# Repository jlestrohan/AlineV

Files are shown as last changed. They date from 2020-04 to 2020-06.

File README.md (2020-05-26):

# Alinea

### Autonomous Low Impact Networked Exploration Android

Protype built around:

- Caterpillar Chassis: https://www.ebay.fr/itm/292912268306

This device is aimed to map any indoor space, cartography its environment, 
while taking all sort of environmental datas, air quality, temperature, humidity,
etc...
Equipped with a 640x400 camera it can be effective in unaccessible areas as a
forefront explorer.

It is totally autonomous, althought it can be remotely controlled (Wifi/Bluetooth)
and will always try to control its whereabouts so that it can safely return back
to where it started.

#### Microcontrollers:

*  Nucleo STM32G474RE 172Mhz (main controller)
*  ESP32 (Wifi)
*  Alternate ESP8266 version

#### Sensors:

*  LM393 x2     Independant caterpillar speed sensors
*  SHR-04 x3    Ultrasonic Distance Sensors
*  CMPS12       Telemetry ToF magnetometer sensor
*  Buzzer       Start up music (not avail in esp8266 version))
*  BME280       Temperature/Humidity/Pressure
*  UV Leds simulating huge UV C lamps (200 ~ 280nm)

#### Batteries:
*  Lipo 4S/65C Battery for over one hour autonomy  

#### Motors:
*   2x PWM stepper motors controlling each caterpillar.

#### Displays:
*  16x2 LCD I2C Display module
  
#### Cloud/Gateway:
*  Able to send data over to it's gateway and/or MQTT endpoint
*  Video streaming included

### Main features
#### Autonomous behaviour
    The device is able to recon its environment. Once started it initializes 
    itself and starts mapping the region around him, and records any of it's 
    movement on a AWS Dynamodb. The datas are processed thru a graphical 
    interface (redash) that offers some visuals.
    
It's integrated movement detection device makes it a perfect candidate for 
security patrol device which is then able to patrol along a predefined path or 
totally autonomously.

The motors are intelligently controlled so the device can respond to about every
critical event that can happen:

    * it will detect any derivation from the current heading and adjust its 
        trajectory accordingly until it meets an obstacle.if one of the caterpillar 
        is skidding for some reason and the android is starting to lose its heading,
        it will detect the fault and try to correct its trajectory by regulating 
        the motors power accordingly, guided by its inbuilt CMPS12 mag sensor
    *  it is able to record every single movement it makes so it is easy for it to
        just turn back and come back to a previous location with a relatively good
        accuracy (not implemented yet)
    * Once an obstacle has been detected from the front or rear sensors (bound to
        where it's actually headed) it will compute the best directional decision to 
        take next according to the side sensors data.
    * if it meets some kind of hole or dangerous terrain that could have dire 
        consequences upon the mission, it will try to avoid the obstacle and keep
        the previous heading once the obstacle have been overtaken, thanks to a 
        couple of obstacle sensors located underneath the chassis that will guard
        the device from falling from too height for instance. Thus it will also 
        deactivate if it detects any lift off or any foreign action taken against
        it, while keeping the video monitor active (if previously setup)
    * To preserve a constant speed and guarantee an accurate mapping of the place it
        is operating in, the device is equipped with a gyroscope/accelerometer that
        will let it adjust its speed either on flat or upward/downward sloping 
        terrains for instance. It will also detect it's current levelling and adapt
        the datas accordingly.
    * according to what has been defined when the device was setup and started, it can adopt
        different behaviours according to any event that may occur:
        
        ie:
            1.  one of the environmental sensor gets some critical values, is offline...
            2.  battery getting low, shall it return or stop ?
            3.  mapping completed, no known unmapped surface left, mapping lost...
            4.  control command received from the remote operator
            5.  data processing compromised (SD card full, no connectivity..)
            6.  movement or dire condition detected that requires human intervention
            7.  in the case of patrol mode, detection of some unattended event...
            etc...
            
    To be continued, edited.. and coded.... this project is far from over but 
    still in a very presentable way.
        
        Beside robotics, it is a real connected thing!

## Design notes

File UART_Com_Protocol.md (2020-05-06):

# UART Communication protocol

### Protocol convention for com between STM32 and ESP8266

Custom and simplified Implementation of the HDLC Protocol (High-Level Data Link Control).
The communication between the STM32 and the ESP32 is a full-duplex bi-directional
data exchange "best-effort" mode (for now).

However as the lines between both MCU are very short, fixed, and thus very little prone to errors,
all the coding eforts are currently focused on data transmission to the cloud, and building the IA.

Encapsulated data is serialized JSON data:

#### Commands:

All datas/commands/sensors id etc..  MUST be defined each side and double checked.
For the sake of a lighter payload we just send very little information thru the UART.
Bitwise flags are used to be able to send several commands to several devices in a single
communication process.

Any MCU is able to either send data on its own. In the case of the STM32 we consider
that every data sent out of request is something he asks the ESP32 to relay to the cloud, unless
previously asked by the ESP32.

### General
    ##### Devices infos (variables included in all JSON)
    
    TIMESTAMP       (if no NTP is available at any point, this field will be -1 - both devices share the same clock, stm32 requests the esp anytime to have this updated)
    DEVICE_UUID     32 bits UUID
    UPTIME          in ms ticks

### STM32 
    ##### Addressable Devices: (uint16_t DeviceFlag)
    
        MOTOR_LEFT              =   1 << 0      /* control & speed info */
        MOTOR_RIGHT             =   1 << 1      /* control & speed info */
        FRONT_ULTRASONIC        =   1 << 2      /* control (on/off) & data (beware the fast acquisition vs the slow transmission) */
        BACK_ULTRASONIC         =   1 << 3      /* see above */
        BOTTOM_ULTRASONIC       =   1 << 4      /* see above */
        FRONT_SENSOR_SERVO      =   1 << 5      /* control & position (pwm value) */
        BMP280_SENSOR           =   1 << 6      /* control (on/off) & pressure information */
        MPU6050_SENSOR          =   1 << 7
        SDCARD_DEVICE           =   1 << 8      /* read file, status, control */     
        LED_ONBOARD             =   1 << 9
        LED_UART_EXTERNAL       =   1 << 10
        
        CORE_SYSTEM_STATUS      =   1 << 14     /* when requested infos are temperature, device uuid, active threads, avg load, uptime, etc etc... */
        CORE_SYSTEM_DEEPSLEEP   =   1 << 15     /* special flag, will take precedence over all the rest, when received the device goes into deepsleep mode!! */
        
### ESP32
    ##### Addressable Devices: (uint16_t DeviceFlag)
    
        BUZZER_DEVICE           =   1 << 0      /* play tune command essentially */
        
        CORE_SYSTEM_DATA        =   1 << 14     /* when requested infos are temperature, device uuid, active threads, avg load, uptime, etc etc... */
        CORE_SYSTEM_DEEPSLEEP   =   1 << 15     /* special flag, will take precedence over all the rest, when received the device goes into deepsleep mode!! */

### Common Actions: 
    ##### Actions(uint16_r cmdActionsFlag)
    
        CONTROL_OFF             =   1 << 0      /* Commands the device to turn on */
        CONTROL_ON              =   1 << 1      /* Commands the device to turn off - Beware, nav control will always have the last word. If you ask the bottom sensor 
                                                    to turn off, the Nav Control will immediately stop the engines to avoid putting the robot in a situation of danger.
                                                    Also, if you command the right motor to turn off, the robot will not hit something left if it detects an obstacle */
        REQ_STATUS              =   1 << 2      /* requests a full status, payload may vary according to the available data */
        REQ_DATA                =   1 << 3      /* requests data acquisition & transmission for the selected device(s)
        SEND_DATA               =   1 << 4      /* Informs the device that arguments are available along with the command.. ie Buzzer, play tune 6
        REQ_READY               =   1 << 5      /* requests the other MCU if it is ready to accept communications - adapt code accordingly */
        ACK_READY               =   1 << 6      /* acknowledge ready status */
        
### JSON Example:

    STM to >ESP32 example:
    {
        "Timestamp":    1588746512,
        "Uptime":   124098,
        deviceFlag: 1,      /* buzzer */
        actionFlags: 4,     /* we send data to the device */
        data:[
            "playtune": 3   /* will command the device to play tune 3 */
        ]

    to be edited ...
{

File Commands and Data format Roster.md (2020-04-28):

## ESP32 <-> STM32 Commands and Data format Roster

Aside from the proprietary protocol used to let both micro-controllers share data in a full duplex bi-directional way, the following conventions have been setup:

### commands:

All commands are to be included between [CMD:(sha256)] **command here** [/CMD] tags

##### <u>emitted by the STM32 to ESP32:</u>

* **tune** *tunetype* *prioritary*
  *  will command the ESP32 to play the selected tune. 
  * *tunetype*: (string) name of the tune
  * *prioritary*: if true, this flag will order the ESP32 to immediately play the tune even if something else is playing
* **tune** *tunelist* - will command the ESP32 to send back an array of the tunes available
  * tunelist: keyword

##### <u>emitted by the ESP32 to STM32:</u>

- **restart**
  - restarts the rover, going thru all initialization process
- **sleep**
  - commands the STM32 to go into deepsleep mode to save battery
  - will be woke up either by a press on the user button, either any event incoming via network still to be defined
  - that command will also be invoked when the LiPo battery sensor detects a weak battery, in order to avoid the destruction of the lipo's cells. In such case a recognizable tune will also be played by the buzzer to inform the driver that the Lipo has to be changed.
- **wakeup**
  - commands the STM32 to exit deepsleep mode and become fully operational again
* **motion** *forward/backward* *milliseconds* *<u>speed</u>*
  * commands the rover to start moving backward or forward for x millis at the optional speed between 1 to 100 (0 will return a bad command error)
* **motion** *left/right millis <u>speed</u>*
  * commands the rover to start turning left or right for x millis at the optional speed 1-100 (0 would return a bad command error)
* **motion** *azimuth milliseconds <u>speed</u>*
  * commands the rover to start moving toward the azimuth given in degrees (magnetic) for x millis at the speed of (1-100, 0 returning a bad command error)
* **motion** *stop*
  * will immediately stop the rover commanding the motors to idle

    All motion commands will still be driven by the obstacle detection sensors and the rover will never endanger itself, thus stopping itself even if it has 
    been commanded to move. 
  
* **lcd** *clear*
  * clears the LCD display
* **lcd** *cursor X Y*
  * sets LCD cursor to X Y
* **lcd** *print text*
  * prints "text" to the display, trimming anything over 16 chars

### datas:

All commands are to be included between [DTA:(sha256)] **{json data here}** [/DTA] tags. 

Datas are JSON preformatted and ready to be passed to the ESP32 for direct forwarding to MQTT service thru communication protocols available (BLE, BT, WiFi etc..)

No data is sent from the ESP32 to the STM32, all eventual data needed is included in the commands if applicable.

All SHA256 calculations are made counting every character included between the tags with brackets.

json format for STM general status:

```
{"STATE": {
	"timestamp": 1588046942,
	"free_heap": 2140,
    "ram_used": 10354,
    "ram_free": 595026,
    "sensor_voltage": 5,
    "core_temp_c": 47,
    "firmware_version": "1.12c",
    "last_updated": "2020-04-28T05:13:48",
    "device_uuid": "123e4567-e89b-12d3-a456-426655440000",
    },
 } 

```

	json format for STM Sensor data (example)

```
{"DATA": {
	"timestamp": 1588046942,
    "device_uuid": "123e4567-e89b-12d3-a456-426655440000",
    "SENSOR": {
    		"sensorType": "gaz",
    		"module_id": "12BDE54",
    		"value": 23,
    		"unit": "C"
    	},
    },
 } 

```

		json format for STM ACK result:

```
{"RESULT": {
	"timestamp": 1588046942,
    "device_uuid": "123e4567-e89b-12d3-a456-426655440000",
    "RESULT": {
    		"command": "motion forward 15000",
    		"result": "completed",
    		"time_completed_ms": 23254,
    	},
    },
 } 

```

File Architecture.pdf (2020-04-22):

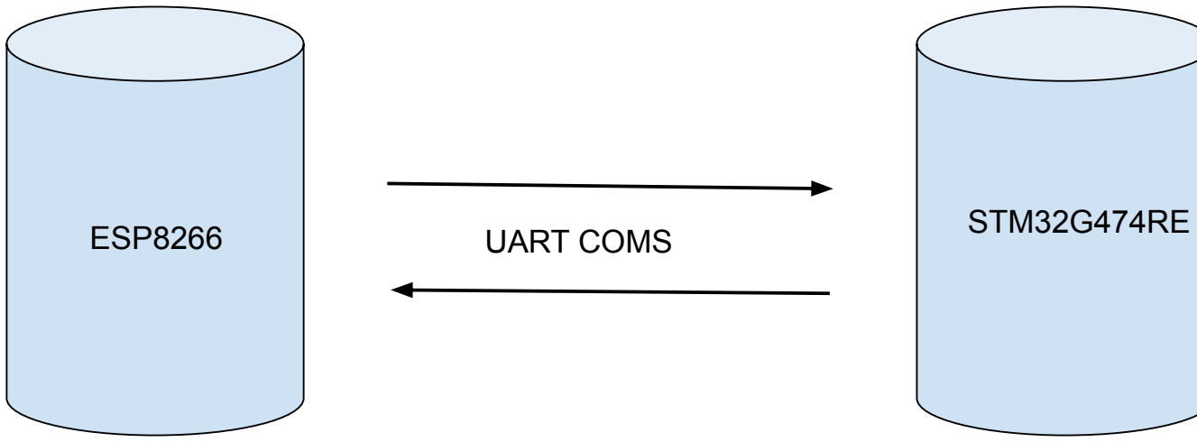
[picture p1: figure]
ESP8266; STM32G474RE UART COMS

TELNET

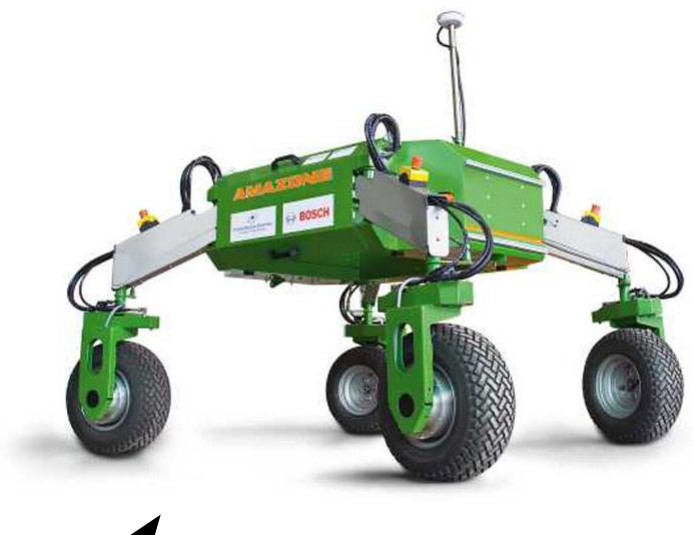
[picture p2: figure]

Motion Ctrl

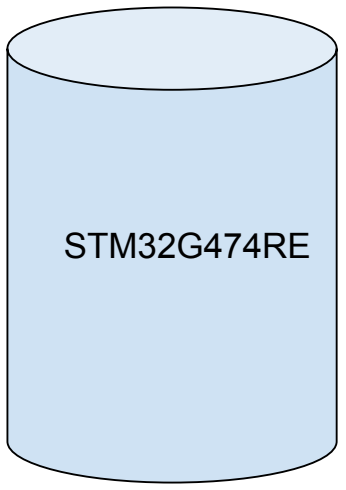
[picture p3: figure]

Sensors

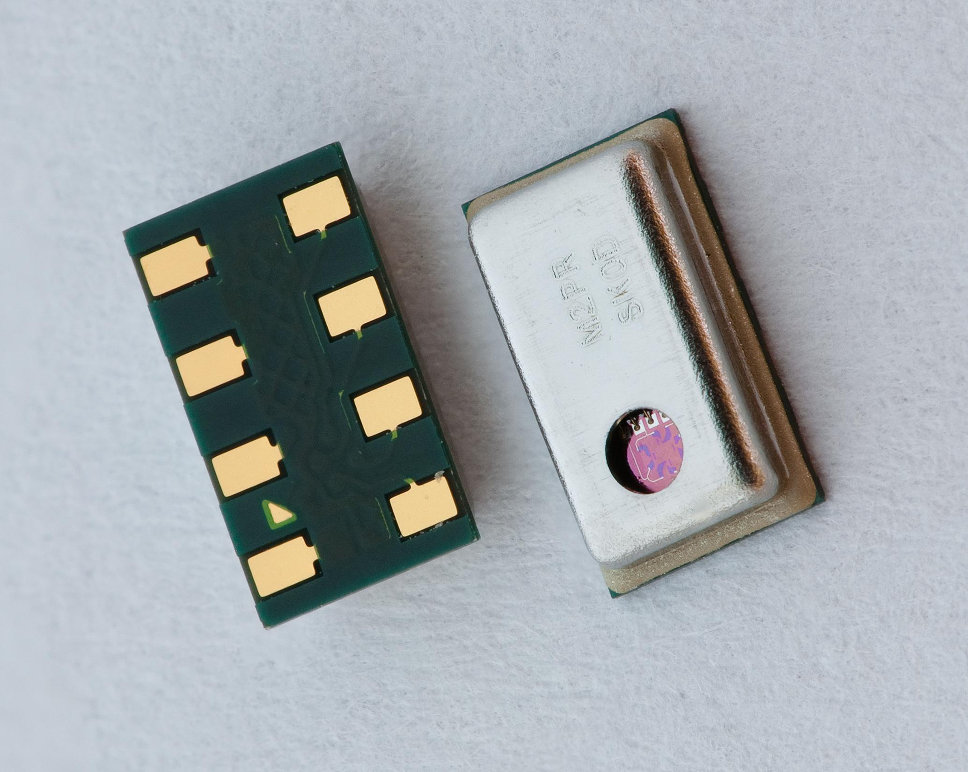
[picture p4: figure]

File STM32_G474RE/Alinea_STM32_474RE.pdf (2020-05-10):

## Alinea_STM32_474RE Project Configuration Report

# 1. Description

## 1.1. Project

Project Name | Alinea_STM32_474RE
Board Name | NUCLEO-G474RE
Generated with: | STM32CubeMX 5.6.1
Date | 05/08/2020

## 1.2. MCU

MCU Series | STM32G4
MCU Line | STM32G4x4
MCU name | STM32G474RETx
MCU Package | LQFP64
MCU Pin number | 64

# 2. Pinout Configuration

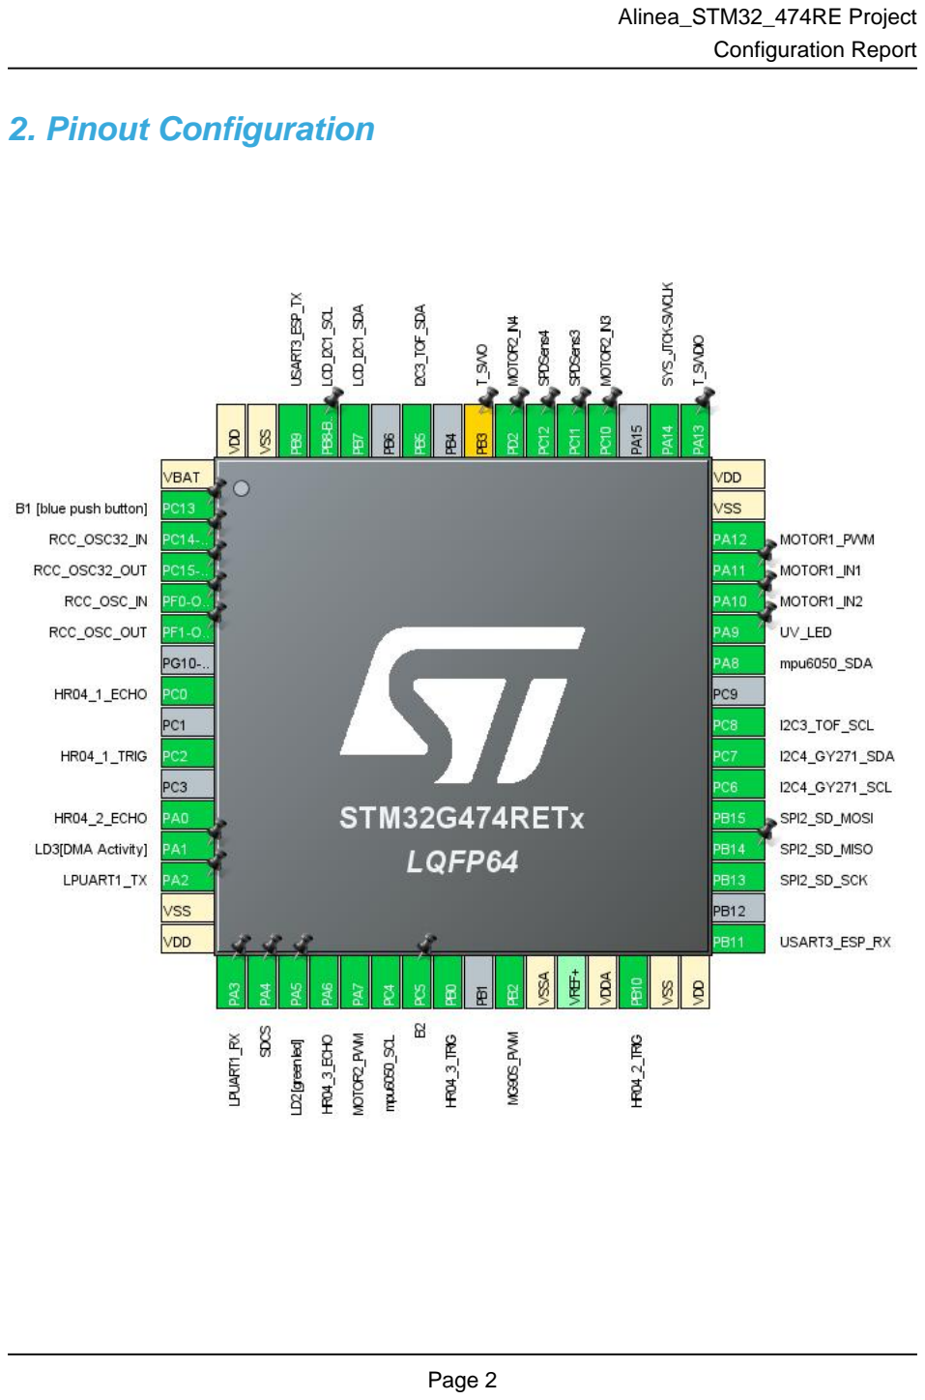
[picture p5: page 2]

# 3. Pins Configuration

Pin Number LQFP64 | Pin Name (function after reset) | Pin Type | Alternate Function(s) | Label
1 | VBAT | Power
2 | PC13 | I/O | GPIO_EXTI13 | B1 [blue push button]
3 | PC14-OSC32_IN | I/O | RCC_OSC32_IN
4 | PC15-OSC32_OUT | I/O | RCC_OSC32_OUT
5 | PF0-OSC_IN | I/O | RCC_OSC_IN
6 | PF1-OSC_OUT | I/O | RCC_OSC_OUT
8 | PC0 | I/O | TIM1_CH1 | HR04_1_ECHO
10 | PC2 | I/O | TIM1_CH3 | HR04_1_TRIG
12 | PA0 | I/O | TIM2_CH1 | HR04_2_ECHO
13 | PA1 * | I/O | GPIO_Output | LD3[DMA Activity]
14 | PA2 | I/O | LPUART1_TX
15 | VSS | Power
16 | VDD | Power
17 | PA3 | I/O | LPUART1_RX
18 | PA4 * | I/O | GPIO_Output | SDCS
19 | PA5 * | I/O | GPIO_Output | LD2 [green led]
20 | PA6 | I/O | TIM3_CH1 | HR04_3_ECHO
21 | PA7 | I/O | TIM17_CH1 | MOTOR2_PWM
22 | PC4 | I/O | I2C2_SCL | mpu6050_SCL
23 | PC5 | I/O | GPIO_EXTI5 | B2
24 | PB0 | I/O | TIM3_CH3 | HR04_3_TRIG
26 | PB2 | I/O | TIM5_CH1 | MG90S_PWM
27 | VSSA | Power
29 | VDDA | Power
30 | PB10 | I/O | TIM2_CH3 | HR04_2_TRIG
31 | VSS | Power
32 | VDD | Power
33 | PB11 | I/O | USART3_RX | USART3_ESP_RX
35 | PB13 | I/O | SPI2_SCK | SPI2_SD_SCK
36 | PB14 | I/O | SPI2_MISO | SPI2_SD_MISO
37 | PB15 | I/O | SPI2_MOSI | SPI2_SD_MOSI
38 | PC6 | I/O | I2C4_SCL | I2C4_GY271_SCL
39 | PC7 | I/O | I2C4_SDA | I2C4_GY271_SDA
40 | PC8 | I/O | I2C3_SCL | I2C3_TOF_SCL
42 | PA8 | I/O | I2C2_SDA | mpu6050_SDA
43 | PA9 * | I/O | GPIO_Output | UV_LED

Pin Number LQFP64 | Pin Name (function after reset) | Pin Type | Alternate Function(s) | Label
44 | PA10 * | I/O | GPIO_Output | MOTOR1_IN2
45 | PA11 * | I/O | GPIO_Output | MOTOR1_IN1
46 | PA12 | I/O | TIM16_CH1 | MOTOR1_PWM
47 | VSS | Power
48 | VDD | Power
49 | PA13 | I/O | SYS_JTMS-SWDIO | T_SWDIO
50 | PA14 | I/O | SYS_JTCK-SWCLK
52 | PC10 * | I/O | GPIO_Output | MOTOR2_IN3
53 | PC11 | I/O | GPIO_EXTI11 | SPDSens3
54 | PC12 | I/O | GPIO_EXTI12 | SPDSens4
55 | PD2 * | I/O | GPIO_Output | MOTOR2_IN4
56 | PB3 ** | I/O | SYS_JTDO-SWO | T_SWO
58 | PB5 | I/O | I2C3_SDA | I2C3_TOF_SDA
60 | PB7 | I/O | I2C1_SDA | LCD_I2C1_SDA
61 | PB8-BOOT0 | I/O | I2C1_SCL | LCD_I2C1_SCL
62 | PB9 | I/O | USART3_TX | USART3_ESP_TX
63 | VSS | Power
64 | VDD | Power

## * The pin is affected with an I/O function ** The pin is affected with a peripheral function but no peripheral mode is activated

# 4. Clock Tree Configuration

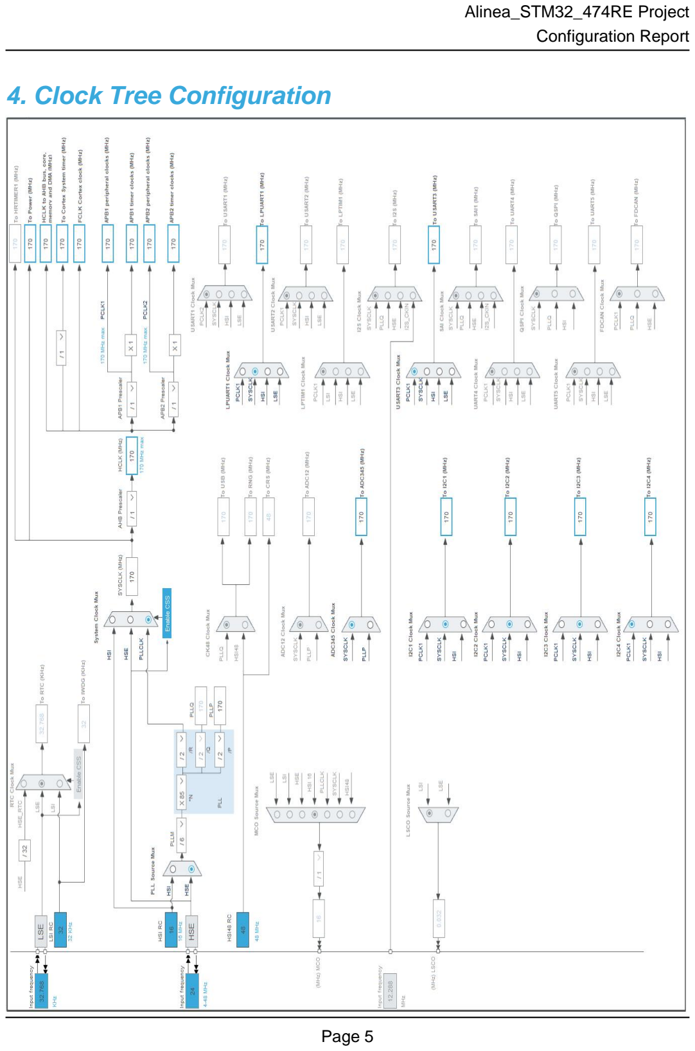
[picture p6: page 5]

# 5. Software Project

## 5.1. Project Settings

Name | Value
Project Name | Alinea_STM32_474RE
Project Folder | F:\Documents\STM32CubeWSP\alinea\STM32_G474RE
Toolchain / IDE | STM32CubeIDE
Firmware Package Name and Version | STM32Cube FW_G4 V1.2.0

## 5.2. Code Generation Settings

Name | Value
STM32Cube MCU packages and embedded software | Copy only the necessary library files
Generate peripheral initialization as a pair of '.c/.h' files | Yes
Backup previously generated files when re-generating | No
Delete previously generated files when not re-generated | Yes
Set all free pins as analog (to optimize the power consumption) | No

# 6. Power Consumption Calculator report

### 6.1. Microcontroller Selection

Series | STM32G4
Line | STM32G4x4
MCU | STM32G474RETx
Datasheet | DS12288_Rev0

### 6.2. Parameter Selection

Temperature | 25
Vdd | 3.0

### 6.3. Battery Selection

Battery | Li-SOCL2(A3400)
Capacity | 3400.0 mAh
Self Discharge | 0.08 %/month
Nominal Voltage | 3.6 V
Max Cont Current | 100.0 mA
Max Pulse Current | 200.0 mA
Cells in series | 1
Cells in parallel | 1

## 6.4. Sequence

Step | Step1 | Step2
Mode | RUN | STOP1
Vdd | 3.0 | 3.0
Voltage Source | Battery | Battery
Range | Range1-Boost | NoRange
Fetch Type | FLASH/DualBank/ART | NA
CPU Frequency | 170 MHz | 0 Hz
Clock Configuration | HSE BYP PLL | ALL CLOCKS OFF
Clock Source Frequency | 4 MHz | 0 Hz

### Peripherals

Additional Cons. | 0 mA | 0 mA
Average Current | 29.5 mA | 80.5 µA
Duration | 0.1 ms | 0.9 ms
DMIPS | 213.0 | 0.0
Ta Max | 124.25 | 129.98
Category | In DS Table | In DS Table

## 6.5. RESULTS

Sequence Time | 1 ms | Average Current | 3.02 mA
Battery Life | 1 month, 16 days, 9 hours | Average DMIPS | 212.5 DMIPS

## 6.6. Chart

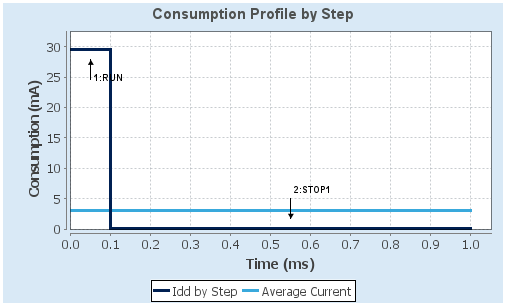
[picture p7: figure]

# 7. IPs and Middleware Configuration

# 7.1. ADC5

## mode: Temperature Sensor Channel mode: Vbat Channel mode: Vrefint Channel 7.1.1. Parameter Settings:

### ADC_Settings:

Clock Prescaler | Asynchronous clock mode divided by 1
Resolution | ADC 12-bit resolution
Data Alignment | Right alignment
Gain Compensation | 0
Scan Conversion Mode | Enabled
End Of Conversion Selection | End of single conversion
Low Power Auto Wait | Disabled
Continuous Conversion Mode | Enabled *
Discontinuous Conversion Mode | Disabled
DMA Continuous Requests | Disabled
Overrun behaviour | Overrun data preserved

### ADC_Regular_ConversionMode:

Enable Regular Conversions | Enable
Enable Regular Oversampling | Disable
Number Of Conversion | 3 *
External Trigger Conversion Source | Regular Conversion launched by software
External Trigger Conversion Edge | None
Rank | 1
Channel | Channel Temperature Sensor
Sampling Time | 92.5 Cycles *
Offset Number | No offset
Rank | 2 *
Channel | Channel Vbat *
Sampling Time | 92.5 Cycles *
Offset Number | No offset
Rank | 3 *
Channel | Channel Vrefint *
Sampling Time | 92.5 Cycles *
Offset Number | No offset

### ADC_Injected_ConversionMode:

Enable Injected Conversions | Disable

### Analog Watchdog 1:

Enable Analog WatchDog1 Mode | false

### Analog Watchdog 2:

Enable Analog WatchDog2 Mode | false

### Analog Watchdog 3:

Enable Analog WatchDog3 Mode | false

# 7.2. GPIO

# 7.3. I2C1

## I2C: I2C 7.3.1. Parameter Settings:

### Timing configuration:

Custom Timing | Disabled
I2C Speed Mode | Standard Mode
I2C Speed Frequency (KHz) | 100
Rise Time (ns) | 0
Fall Time (ns) | 0
Coefficient of Digital Filter | 0
Analog Filter | Enabled
Timing | 0x30A0A7FB *

### Slave Features:

Clock No Stretch Mode | Disabled
General Call Address Detection | Disabled
Primary Address Length selection | 7-bit
Dual Address Acknowledged | Disabled
Primary slave address | 0

# 7.4. I2C2

## I2C: I2C 7.4.1. Parameter Settings:

### Timing configuration:

Custom Timing | Disabled

I2C Speed Mode | Standard Mode
I2C Speed Frequency (KHz) | 100
Rise Time (ns) | 0
Fall Time (ns) | 0
Coefficient of Digital Filter | 0
Analog Filter | Enabled
Timing | 0x30A0A7FB *

### Slave Features:

Clock No Stretch Mode | Disabled
General Call Address Detection | Disabled
Primary Address Length selection | 7-bit
Dual Address Acknowledged | Disabled
Primary slave address | 0

# 7.5. I2C3

## I2C: I2C 7.5.1. Parameter Settings:

### Timing configuration:

Custom Timing | Disabled
I2C Speed Mode | Fast Mode *
I2C Speed Frequency (KHz) | 400
Rise Time (ns) | 0
Fall Time (ns) | 0
Coefficient of Digital Filter | 0
Analog Filter | Enabled
Timing | 0x10802D9B *

### Slave Features:

Clock No Stretch Mode | Disabled
General Call Address Detection | Disabled
Primary Address Length selection | 7-bit
Dual Address Acknowledged | Disabled
Primary slave address | 0

# 7.6. I2C4

## I2C: I2C

## 7.6.1. Parameter Settings:

### Timing configuration:

Custom Timing | Disabled
I2C Speed Mode | Standard Mode
I2C Speed Frequency (KHz) | 100
Rise Time (ns) | 0
Fall Time (ns) | 0
Coefficient of Digital Filter | 0
Analog Filter | Enabled
Timing | 0x30A0A7FB *

### Slave Features:

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

# 7.7. LPUART1

## Mode: Asynchronous 7.7.1. Parameter Settings:

### Basic Parameters:

Baud Rate | 115200 *
Word Length | 8 Bits (including Parity)
Parity | None
Stop Bits | 1

### Advanced Parameters:

Data Direction | Receive and Transmit
Single Sample | Disable
Prescaler | clock /1
Fifo Mode | FIFO mode disable
Txfifo Threshold | 1 eighth full configuration
Rxfifo Threshold | 1 eighth full configuration

### Advanced Features:

TX Pin Active Level Inversion | Disable
RX Pin Active Level Inversion | Disable
Data Inversion | Disable
TX and RX pins Swapping | Disable

Overrun | Enable
DMA on RX Error | Enable
MSB First | Disable

# 7.8. RCC

## High Speed Clock (HSE): Crystal/Ceramic Resonator Low Speed Clock (LSE) : Crystal/Ceramic Resonator 7.8.1. Parameter Settings:

### System Parameters:

VDD voltage (V) | 3.3
Instruction Cache | Enabled
Prefetch Buffer | Disabled
Data Cache | Enabled
Flash Latency(WS) | 8WS (7 CPU cycle)

### RCC Parameters:

HSI Calibration Value | 64
HSE Startup Timout Value (ms) | 100
LSE Startup Timout Value (ms) | 5000

### Power Parameters:

Power Regulator Voltage Scale | Power Regulator Voltage Scale 1 boost

### Peripherals Clock Configuration:

Generate the peripherals clock configuration | TRUE

# 7.9. SPI2

## Mode: Full-Duplex Master 7.9.1. Parameter Settings:

### Basic Parameters:

Frame Format | Motorola
Data Size | 8 Bits *
First Bit | MSB First

### Clock Parameters:

Prescaler (for Baud Rate) | 4 *
Baud Rate | 42.5 MBits/s *
Clock Polarity (CPOL) | Low

Clock Phase (CPHA) | 1 Edge

### Advanced Parameters:

CRC Calculation | Disabled
NSSP Mode | Enabled
NSS Signal Type | Software

# 7.10. SYS

## Debug: Serial Wire Timebase Source: TIM7 mode: save power of non-active UCPD - deactive Dead Battery pull-up

# 7.11. TIM1

## Slave Mode: Reset Mode Trigger Source: TI1FP1 Clock Source : Internal Clock Channel1: Input Capture direct mode Channel2: Input Capture indirect mode Channel3: PWM Generation CH3 7.11.1. Parameter Settings:

### Counter Settings:

Prescaler (PSC - 16 bits value) | 170-1 *
Counter Mode | Up
Dithering | Disable
Counter Period (AutoReload Register - 16 bits value ) | 0xffff-1 *
Internal Clock Division (CKD) | No Division
Repetition Counter (RCR - 16 bits value) | 0
auto-reload preload | Disable
Slave Mode Controller | Reset Mode

### Trigger Output (TRGO) Parameters:

Master/Slave Mode (MSM bit) | Disable (Trigger input effect not delayed)
Trigger Event Selection TRGO | Reset (UG bit from TIMx_EGR)
Trigger Event Selection TRGO2 | Reset (UG bit from TIMx_EGR)

### Break And Dead Time management - BRK Configuration:

BRK State | Disable
BRK Polarity | High
BRK Filter (4 bits value) | 0

BRK Sources Configuration
- Digital Input | Disable
- COMP1 | Disable
- COMP2 | Disable
- COMP3 | Disable
- COMP4 | Disable
- COMP5 | Disable
- COMP6 | Disable
- COMP7 | Disable

### Break And Dead Time management - BRK2 Configuration:

BRK2 State | Disable
BRK2 Polarity | High
BRK2 Filter (4 bits value) | 0
BRK2 Sources Configuration
- Digital Input | Disable
- COMP1 | Disable
- COMP2 | Disable
- COMP3 | Disable
- COMP4 | Disable
- COMP5 | Disable
- COMP6 | Disable
- COMP7 | Disable

### Break And Dead Time management - Output Configuration:

Automatic Output State | Disable
Off State Selection for Run Mode (OSSR) | Disable
Off State Selection for Idle Mode (OSSI) | Disable
Lock Configuration | Off

### Clear Input:

Clear Input Source | Disable

### Pulse On Compare ( Common for Channel 3 and 4 ):

Pulse Width Prescaler | 0
Pulse Width | 0

### Input Capture Channel 1:

Polarity Selection | Rising Edge
IC Selection | Direct
Prescaler Division Ratio | No division
Input Filter (4 bits value) | 0

### Input Capture Channel 2:

Polarity Selection | Falling Edge *
IC Selection | Indirect
Prescaler Division Ratio | No division

### PWM Generation Channel 3:

Mode | PWM mode 1
Pulse (16 bits value) | 10 *
Output compare preload | Enable
Fast Mode | Enable *
CH Polarity | High
CH Idle State | Reset

# 7.12. TIM2

## Slave Mode: Reset Mode Trigger Source: TI1FP1 Clock Source : Internal Clock Channel1: Input Capture direct mode Channel2: Input Capture indirect mode Channel3: PWM Generation CH3 7.12.1. Parameter Settings:

### Counter Settings:

Prescaler (PSC - 16 bits value) | 170-1 *
Counter Mode | Up
Dithering | Disable
Counter Period (AutoReload Register - 32 bits value ) | 0xffff-1 *
Internal Clock Division (CKD) | No Division
auto-reload preload | Disable
Slave Mode Controller | Reset Mode

### Trigger Output (TRGO) Parameters:

Master/Slave Mode (MSM bit) | Disable (Trigger input effect not delayed)
Trigger Event Selection TRGO | Reset (UG bit from TIMx_EGR)

### Clear Input:

Clear Input Source | Disable

### Pulse On Compare ( Common for Channel 3 and 4 ):

Pulse Width Prescaler | 0
Pulse Width | 0

### Input Capture Channel 1:

Polarity Selection | Rising Edge
IC Selection | Direct
Prescaler Division Ratio | No division
Input Filter (4 bits value) | 0

### Input Capture Channel 2:

Polarity Selection | Falling Edge *
IC Selection | Indirect
Prescaler Division Ratio | No division

### PWM Generation Channel 3:

Mode | PWM mode 1
Pulse (32 bits value) | 10 *
Output compare preload | Enable
Fast Mode | Enable *
CH Polarity | High

# 7.13. TIM3

## Slave Mode: Reset Mode Trigger Source: TI1FP1 Clock Source : Internal Clock Channel1: Input Capture direct mode Channel2: Input Capture indirect mode Channel3: PWM Generation CH3 7.13.1. Parameter Settings:

### Counter Settings:

Prescaler (PSC - 16 bits value) | 170-1 *
Counter Mode | Up
Dithering | Disable
Counter Period (AutoReload Register - 16 bits value ) | 0xffff-1 *
Internal Clock Division (CKD) | No Division
auto-reload preload | Disable
Slave Mode Controller | Reset Mode

### Trigger Output (TRGO) Parameters:

Master/Slave Mode (MSM bit) | Disable (Trigger input effect not delayed)
Trigger Event Selection TRGO | Reset (UG bit from TIMx_EGR)

### Clear Input:

Clear Input Source | Disable

### Pulse On Compare ( Common for Channel 3 and 4 ):

Pulse Width Prescaler | 0
Pulse Width | 0

### Input Capture Channel 1:

Polarity Selection | Rising Edge
IC Selection | Direct
Prescaler Division Ratio | No division
Input Filter (4 bits value) | 0

### Input Capture Channel 2:

Polarity Selection | Falling Edge *
IC Selection | Indirect
Prescaler Division Ratio | No division

### PWM Generation Channel 3:

Mode | PWM mode 1
Pulse (16 bits value) | 10 *
Output compare preload | Enable
Fast Mode | Enable *
CH Polarity | High

# 7.14. TIM5

## Channel1: PWM Generation CH1 7.14.1. Parameter Settings:

### Counter Settings:

Prescaler (PSC - 16 bits value) | 3400-1 *
Counter Mode | Up
Dithering | Disable
Counter Period (AutoReload Register - 32 bits value ) | 1000-1 *
Internal Clock Division (CKD) | No Division
auto-reload preload | Disable

### Trigger Output (TRGO) Parameters:

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

### Clear Input:

Clear Input Source | Disable

### Pulse On Compare ( Common for Channel 3 and 4 ):

Pulse Width Prescaler | 0
Pulse Width | 0

### PWM Generation Channel 1:

Mode | PWM mode 1
Pulse (32 bits value) | 0
Output compare preload | Enable

Fast Mode | Disable
CH Polarity | High

# 7.15. TIM16

## mode: Activated Channel1: PWM Generation CH1 7.15.1. Parameter Settings:

### Counter Settings:

Prescaler (PSC - 16 bits value) | 17000-1 *
Counter Mode | Up
Dithering | Disable
Counter Period (AutoReload Register - 16 bits value ) | 100-1 *
Internal Clock Division (CKD) | No Division
Repetition Counter (RCR - 8 bits value) | 0
auto-reload preload | Disable

### Break And Dead Time management - BRK Configuration:

BRK State | Disable
BRK Polarity | High
BRK Filter (4 bits value) | 0
BRK Sources Configuration
- Digital Input | Disable
- COMP1 | Disable
- COMP2 | Disable
- COMP3 | Disable
- COMP4 | Disable
- COMP5 | Disable
- COMP6 | Disable
- COMP7 | Disable

### Break And Dead Time management - Output Configuration:

Automatic Output State | Disable
Off State Selection for Run Mode (OSSR) | Disable
Off State Selection for Idle Mode (OSSI) | Disable
Lock Configuration | Off

### PWM Generation Channel 1:

Mode | PWM mode 1
Pulse (16 bits value) | 10 *
Output compare preload | Enable
Fast Mode | Disable

CH Polarity | High
CH Idle State | Reset

# 7.16. TIM17

## mode: Activated Channel1: PWM Generation CH1 7.16.1. Parameter Settings:

### Counter Settings:

Prescaler (PSC - 16 bits value) | 17000-1 *
Counter Mode | Up
Dithering | Disable
Counter Period (AutoReload Register - 16 bits value ) | 100-1 *
Internal Clock Division (CKD) | No Division
Repetition Counter (RCR - 8 bits value) | 0
auto-reload preload | Disable

### Break And Dead Time management - BRK Configuration:

BRK State | Disable
BRK Polarity | High
BRK Filter (4 bits value) | 0
BRK Sources Configuration
- Digital Input | Disable
- COMP1 | Disable
- COMP2 | Disable
- COMP3 | Disable
- COMP4 | Disable
- COMP5 | Disable
- COMP6 | Disable
- COMP7 | Disable

### Break And Dead Time management - Output Configuration:

Automatic Output State | Disable
Off State Selection for Run Mode (OSSR) | Disable
Off State Selection for Idle Mode (OSSI) | Disable
Lock Configuration | Off

### PWM Generation Channel 1:

Mode | PWM mode 1
Pulse (16 bits value) | 10 *
Output compare preload | Enable
Fast Mode | Disable

CH Polarity | High
CH Idle State | Reset

# 7.17. USART3

## Mode: Asynchronous 7.17.1. Parameter Settings:

### Basic Parameters:

Baud Rate | 115200
Word Length | 8 Bits (including Parity)
Parity | None
Stop Bits | 1

### Advanced Parameters:

Data Direction | Receive and Transmit
Over Sampling | 16 Samples
Single Sample | Disable
ClockPrescaler | clock /1
Fifo Mode | Disable
Txfifo Threshold | 1 eighth full configuration
Rxfifo Threshold | 1 eighth full configuration

### Advanced Features:

Auto Baudrate | Disable
TX Pin Active Level Inversion | Disable
RX Pin Active Level Inversion | Disable
Data Inversion | Disable
TX and RX Pins Swapping | Disable
Overrun | Enable
DMA on RX Error | Enable
MSB First | Disable

# 7.18. FATFS

## mode: User-defined 7.18.1. Set Defines:

### Version:

FATFS version | R0.12c

### Function Parameters:

FS_READONLY (Read-only mode) | Disabled
FS_MINIMIZE (Minimization level) | Disabled
USE_STRFUNC (String functions) | Enabled with LF -> CRLF conversion
USE_FIND (Find functions) | Disabled
USE_MKFS (Make filesystem function) | Enabled
USE_FASTSEEK (Fast seek function) | Enabled
USE_EXPAND (Use f_expand function) | Disabled
USE_CHMOD (Change attributes function) | Disabled
USE_LABEL (Volume label functions) | Disabled
USE_FORWARD (Forward function) | Disabled

### Locale and Namespace Parameters:

CODE_PAGE (Code page on target) | Latin 1
USE_LFN (Use Long Filename) | Disabled
MAX_LFN (Max Long Filename) | 255
LFN_UNICODE (Enable Unicode) | ANSI/OEM
STRF_ENCODE (Character encoding) | UTF-8
FS_RPATH (Relative Path) | Disabled

### Physical Drive Parameters:

VOLUMES (Logical drives) | 1
MAX_SS (Maximum Sector Size) | 512
MIN_SS (Minimum Sector Size) | 512
MULTI_PARTITION (Volume partitions feature) | Disabled
USE_TRIM (Erase feature) | Disabled
FS_NOFSINFO (Force full FAT scan) | 0

### System Parameters:

FS_TINY (Tiny mode) | Disabled
FS_EXFAT (Support of exFAT file system) | Disabled
FS_NORTC (Timestamp feature) | Dynamic timestamp
FS_REENTRANT (Re-Entrancy) | Enabled
FS_TIMEOUT (Timeout ticks) | 1000
USE_MUTEX | Disabled
SYNC_t (O/S sync object) | osSemaphoreId_t
FS_LOCK (Number of files opened simultaneously) | 2

## 7.18.2. Advanced Settings:

### User Defined:

Diskio code | User

# 7.19. FREERTOS

## Interface: CMSIS_V2 7.19.1. Config parameters:

### API:

FreeRTOS API | CMSIS v2

### Versions:

FreeRTOS version | 10.2.1
CMSIS-RTOS version | 2.00

### MPU/FPU:

ENABLE_MPU | Disabled
ENABLE_FPU | Enabled *

### Kernel settings:

USE_PREEMPTION | Enabled
CPU_CLOCK_HZ | SystemCoreClock
TICK_RATE_HZ | 1000
MAX_PRIORITIES | 56
MINIMAL_STACK_SIZE | 256 *
MAX_TASK_NAME_LEN | 16
USE_16_BIT_TICKS | Disabled
IDLE_SHOULD_YIELD | Enabled
USE_MUTEXES | Enabled
USE_RECURSIVE_MUTEXES | Enabled
USE_COUNTING_SEMAPHORES | Enabled
QUEUE_REGISTRY_SIZE | 8
USE_APPLICATION_TASK_TAG | Disabled
ENABLE_BACKWARD_COMPATIBILITY | Enabled
USE_PORT_OPTIMISED_TASK_SELECTION | Disabled
USE_TICKLESS_IDLE | Disabled
USE_TASK_NOTIFICATIONS | Enabled
RECORD_STACK_HIGH_ADDRESS | Disabled

### Memory management settings:

Memory Allocation | Dynamic / Static
TOTAL_HEAP_SIZE | 4096 *
Memory Management scheme | heap_4

### Hook function related definitions:

USE_IDLE_HOOK | Disabled
USE_TICK_HOOK | Disabled
USE_MALLOC_FAILED_HOOK | Disabled
USE_DAEMON_TASK_STARTUP_HOOK | Disabled

CHECK_FOR_STACK_OVERFLOW | Disabled

### Run time and task stats gathering related definitions:

GENERATE_RUN_TIME_STATS | Disabled
USE_TRACE_FACILITY | Enabled
USE_STATS_FORMATTING_FUNCTIONS | Disabled

### Co-routine related definitions:

USE_CO_ROUTINES | Disabled
MAX_CO_ROUTINE_PRIORITIES | 2

### Software timer definitions:

USE_TIMERS | Enabled
TIMER_TASK_PRIORITY | 2
TIMER_QUEUE_LENGTH | 10
TIMER_TASK_STACK_DEPTH | 512

### Interrupt nesting behaviour configuration:

LIBRARY_LOWEST_INTERRUPT_PRIORITY | 15
LIBRARY_MAX_SYSCALL_INTERRUPT_PRIORITY | 5

### Added with 10.2.1 support:

MESSAGE_BUFFER_LENGTH_TYPE | size_t
USE_POSIX_ERRNO | Disabled

## 7.19.2. Include parameters:

### Include definitions:

vTaskPrioritySet | Enabled
uxTaskPriorityGet | Enabled
vTaskDelete | Enabled
vTaskCleanUpResources | Enabled *
vTaskSuspend | Enabled
vTaskDelayUntil | Enabled
vTaskDelay | Enabled
xTaskGetSchedulerState | Enabled
xTaskResumeFromISR | Enabled
xQueueGetMutexHolder | Enabled
xSemaphoreGetMutexHolder | Disabled
pcTaskGetTaskName | Disabled
uxTaskGetStackHighWaterMark | Enabled
xTaskGetCurrentTaskHandle | Disabled
eTaskGetState | Enabled
xEventGroupSetBitFromISR | Disabled
xTimerPendFunctionCall | Enabled
xTaskAbortDelay | Disabled

xTaskGetHandle | Disabled
uxTaskGetStackHighWaterMark2 | Disabled

## 7.19.3. Advanced settings:

### Newlib settings (see parameter description first):

USE_NEWLIB_REENTRANT | Disabled

### Project settings (see parameter description first):

Use FW pack heap file | Enabled

### * User modified value

# 8. System Configuration

# 8.1. GPIO configuration

IP | Pin | Signal | GPIO mode | GPIO pull/up pull down

## Max Speed

## User Label

I2C1 | PB7 | I2C1_SDA | Alternate Function Open
Drain
Pull-up | Low | LCD_I2C1_SDA
PB8-BOOT0 | I2C1_SCL | Alternate Function Open
Drain
Pull-up | Low | LCD_I2C1_SCL
I2C2 | PC4 | I2C2_SCL | Alternate Function Open
Drain
Pull-up | Low | mpu6050_SCL
PA8 | I2C2_SDA | Alternate Function Open
Drain
Pull-up | Low | mpu6050_SDA
I2C3 | PC8 | I2C3_SCL | Alternate Function Open
Drain
Pull-up | Low | I2C3_TOF_SCL
PB5 | I2C3_SDA | Alternate Function Open
Drain
Pull-up | Low | I2C3_TOF_SDA
I2C4 | PC6 | I2C4_SCL | Alternate Function Open
Drain
Pull-up | Low | I2C4_GY271_SCL
PC7 | I2C4_SDA | Alternate Function Open
Drain
Pull-up | Low | I2C4_GY271_SDA
LPUART1 | PA2 | LPUART1_TX Alternate Function Push Pull | No pull-up and no pull-down | Low
| PA3 | LPUART1_RX Alternate Function Push Pull | No pull-up and no pull-down | Low
RCC | PC14- OSC32_IN
RCC_OSC32_IN | n/a | n/a | n/a
| PC15- OSC32_OU T | RCC_OSC32_O UT
| | n/a | n/a | n/a
PF0-OSC_IN RCC_OSC_IN | n/a | n/a | n/a
PF1-
OSC_OUT
| | RCC_OSC_OUT | n/a | n/a | n/a
SPI2 | PB13 | SPI2_SCK | Alternate Function Push Pull | No pull-up and no pull-down | Low | SPI2_SD_SCK
| PB14 | SPI2_MISO | Alternate Function Push Pull | No pull-up and no pull-down | Low | SPI2_SD_MISO
| PB15 | SPI2_MOSI | Alternate Function Push Pull | No pull-up and no pull-down | Low | SPI2_SD_MOSI
SYS | PA13 | SYS_JTMS- SWDIO | n/a | n/a | n/a | T_SWDIO
| PA14 | SYS_JTCK- SWCLK | n/a | n/a | n/a
TIM1 | PC0 | TIM1_CH1 | Alternate Function Push Pull | Pull-down * | High * | HR04_1_ECHO
| PC2 | TIM1_CH3 | Alternate Function Push Pull | Pull-down * | Very High
*
| | | | | | HR04_1_TRIG
TIM2 | PA0 | TIM2_CH1 | Alternate Function Push Pull | Pull-down * | High * | HR04_2_ECHO
| PB10 | TIM2_CH3 | Alternate Function Push Pull | No pull-up and no pull-down | Low | HR04_2_TRIG

IP | Pin | Signal | GPIO mode | GPIO pull/up pull down | Max Speed | User Label
TIM3 | PA6 | TIM3_CH1 | Alternate Function Push Pull | Pull-down * | High * | HR04_3_ECHO
| PB0 | TIM3_CH3 | Alternate Function Push Pull | No pull-up and no pull-down | Low | HR04_3_TRIG
TIM5 | PB2 | TIM5_CH1 | Alternate Function Push Pull | No pull-up and no pull-down | Low | MG90S_PWM
TIM16 | PA12 | TIM16_CH1 | Alternate Function Push Pull | No pull-up and no pull-down | Low | MOTOR1_PWM
TIM17 | PA7 | TIM17_CH1 | Alternate Function Push Pull | No pull-up and no pull-down | Low | MOTOR2_PWM
USART3 | PB11 | USART3_RX | Alternate Function Push Pull | No pull-up and no pull-down | Low | USART3_ESP_RX
| PB9 | USART3_TX | Alternate Function Push Pull | Pull-down * | High * | USART3_ESP_TX
Single Mapped Signals | PB3 | SYS_JTDO-SWO | n/a | n/a | n/a | T_SWO
| | | Rising edge trigger detection | Pull-down * | n/a | B1 [blue push button]
| PA1 | GPIO_Output | Output Push Pull | No pull-up and no pull-down | Low | LD3[DMA Activity]
| PA4 | GPIO_Output | Output Push Pull | No pull-up and no pull-down | Low | SDCS
| PA5 | GPIO_Output | Output Push Pull | No pull-up and no pull-down | Low | LD2 [green led]
| PC5 | GPIO_EXTI5 | External Interrupt Mode with Falling edge trigger detection | Pull-up * | n/a | B2
| PA9 | GPIO_Output | Output Push Pull | Pull-up * | Low | UV_LED
| PA10 | GPIO_Output | Output Push Pull | No pull-up and no pull-down | Low | MOTOR1_IN2
| PA11 | GPIO_Output | Output Push Pull | No pull-up and no pull-down | Low | MOTOR1_IN1
| PC10 | GPIO_Output | Output Push Pull | No pull-up and no pull-down | Low | MOTOR2_IN3
| PC11 | GPIO_EXTI11 | External Interrupt Mode with Falling edge trigger detection | Pull-up * | n/a | SPDSens3
| PC12 | GPIO_EXTI12 | External Interrupt Mode with Falling edge trigger detection | Pull-up * | n/a | SPDSens4
| PD2 | GPIO_Output | Output Push Pull | No pull-up and no pull-down | Low | MOTOR2_IN4
GPIO | PC13 | GPIO_EXTI13 | External Interrupt Mode with

# 8.2. DMA configuration

DMA request | Stream | Direction | Priority
I2C1_RX | DMA1_Channel3 | Peripheral To Memory | Low
I2C1_TX | DMA1_Channel4 | Memory To Peripheral | Low
ADC5 | DMA1_Channel1 | Peripheral To Memory | Low

## I2C1_RX: DMA1_Channel3 DMA request Settings:

Mode: | Circular *
Peripheral Increment: | Disable
Memory Increment: | Enable *
Peripheral Data Width: | Byte
Memory Data Width: | Byte

## I2C1_TX: DMA1_Channel4 DMA request Settings:

Mode: | Normal
Peripheral Increment: | Disable
Memory Increment: | Enable *
Peripheral Data Width: | Byte
Memory Data Width: | Byte

## ADC5: DMA1_Channel1 DMA request Settings:

Mode: | Circular *
Peripheral Increment: | Disable
Memory Increment: | Enable *
Peripheral Data Width: | Word *
Memory Data Width: | Word *

# 8.3. NVIC configuration

Interrupt Table | Enable | Preenmption Priority | SubPriority
Non maskable interrupt | true | 0 | 0
Hard fault interrupt | true | 0 | 0
Memory management fault | true | 0 | 0
Prefetch fault, memory access fault | true | 0 | 0
Undefined instruction or illegal state | true | 0 | 0
System service call via SWI instruction | true | 0 | 0
Debug monitor | true | 0 | 0
Pendable request for system service | true | 15 | 0
System tick timer | true | 15 | 0
DMA1 channel1 global interrupt | true | 5 | 0
DMA1 channel3 global interrupt | true | 5 | 0
DMA1 channel4 global interrupt | true | 5 | 0
EXTI line[9:5] interrupts | true | 5 | 0
TIM1 capture compare interrupt | true | 5 | 0
TIM2 global interrupt | true | 5 | 0
TIM3 global interrupt | true | 5 | 0
I2C1 event interrupt / I2C1 wake-up interrupt through EXTI line 23 | true | 5 | 0
I2C1 error interrupt | true | 5 | 0
USART3 global interrupt / USART3 wake-up interrupt through EXTI line 28 | true | 5 | 0
EXTI line[15:10] interrupts | true | 5 | 0
TIM7 global interrupt, DAC2 and DAC4 channel underrun error interrupts | true | 0 | 0
ADC5 global interrupt | true | 5 | 0
LPUART1 global interrupt | true | 5 | 0
PVD/PVM1/PVM2/PVM3/PVM4 interrupts through EXTI lines 16/38/39/40/41 | | unused
Flash global interrupt | | unused
RCC global interrupt | | unused
TIM1 break interrupt and TIM15 global interrupt | | unused
TIM1 update interrupt and TIM16 global interrupt | | unused
TIM1 trigger and commutation interrupts and TIM17 global interrupt | | unused
I2C2 event interrupt / I2C2 wake-up interrupt through EXTI line 24 | | unused
I2C2 error interrupt | | unused
SPI2 global interrupt | | unused
TIM5 global interrupt | | unused

Interrupt Table | Enable | Preenmption Priority | SubPriority
FPU global interrupt | unused
I2C4 event interrupt / I2C4 wake-up interrupt through EXTI line 42 | unused
I2C4 error interrupt | unused
I2C3 event interrupt / I2C3 wake-up interrupt through EXTI line 27 | unused
I2C3 error interrupt | unused

### * User modified value

# 9. Predefined Views - Category view : Current

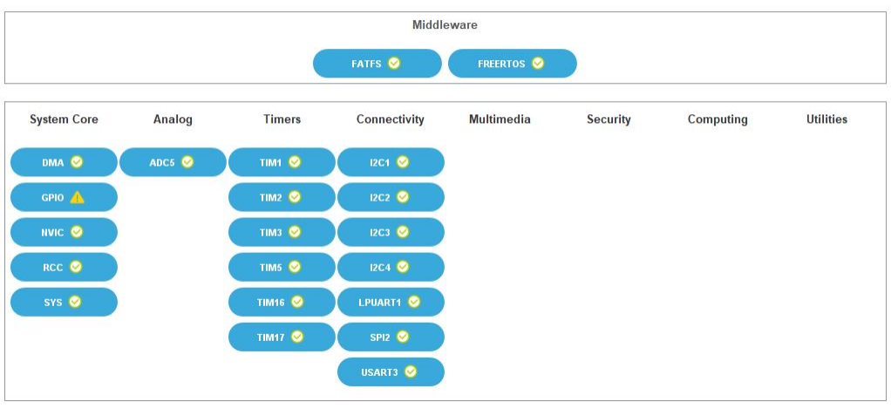
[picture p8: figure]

# 10. Software Pack Report

### 10.1. Software Pack selected

Vendor | Name | Version | Component
STMicroelectronic s | FreeRTOS | 0.0.1 | Class : RTOS Group : Core Version : 10.2.0

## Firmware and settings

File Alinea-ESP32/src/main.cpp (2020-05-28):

/*******************************************************************************************
 * @ Author: Jack Lestrohan
 * @ Create Time: 2020-04-20 16:29:58
 * @ Modified by: Jack Lestrohan
 * @ Modified time: 2020-05-28 07:50:51
 * @ Description:
 *******************************************************************************************/

#include <Arduino.h>
#include <Preferences.h>
#include "autoconnect_service.h"
#include "ota_service.h"
#include "configuration_esp32.h"
#include "remoteDebug_service.h"
#include <FreeRTOS.h>
#include "buzzer_service.h"
#include "stm32Serial_service.h"
#include "ntp_service.h"
#include "buzzer_service.h"
#include "command_service.h"
#include "speed_service.h"
#include "ledstrip_service.h"
#include "data_service.h"

/* reemoving brownout detector */
#include "soc/soc.h"
#include "soc/rtc_cntl_reg.h"

/* functions definitions */
void vBootCounterUpdate();

RemoteDebug Debug;
QueueHandle_t xLedStripCommandQueue;

Preferences preferences;

/**
 * @brief  Main program loop
 * @note   
 * @retval None
 */
void loop()
{
  // nada here everything is FreeRTOS!
}

/* ------------------------------- MAIN SETUP ------------------------------- */
/**
 * @brief  Main setup
 * @note   
 * @retval None
 */
void setup()
{
  WRITE_PERI_REG(RTC_CNTL_BROWN_OUT_REG, 0); //disable brownout detector

  Serial.begin(115200);
  Serial.setDebugOutput(true);

  DEBUG_SERIAL("Starting Program...");

  vBootCounterUpdate();

  uLedStripServiceInit(); /* check */
  uSetupBuzzer();         /* check */
  uSetupCmdParser();
  uSetupAutoConnect(); /* check */
  uSetupRemoteDebug(); /* check */
  uSetupNTPService();  /* check */
  uSetupDataServiceInit();
  uSetupSTM32SerialService(); /* check */
  uSetupSpeedService();
  uSetupOTA();

  lit_status_t ledstatus;
  ledstatus.is_lit = true;
  if (xLedStripCommandQueue)
    xQueueSend(xLedStripCommandQueue, &ledstatus, portMAX_DELAY);

  //const char *cmdRdyESP = "ack restart";
  //if (xQueueCommandParse != NULL)
  /* let's inform the STM that we have just rebooted */
  //xQueueSend(xQueueCommandParse, &cmdRdyESP, portMAX_DELAY);
}

// TODO: connect 2xI2C TOF https://randomnerdtutorials.com/esp32-i2c-communication-arduino-ide/#7

/* ------------------------------ BOOT COUNTER ------------------------------ */
/**
 * @brief  Updates (and print) the boot counter
 * @note   
 * @retval None
 */
void vBootCounterUpdate()
{
  /* we update the boot count counter to know how many times our device has booted */
  preferences.begin("alinev-core", false);
  // Get the counter value, if the key does not exist, return a default value of 0
  // Note: Key name is limited to 15 chars.
  unsigned int boot_counter = preferences.getUInt("boot_counter", 0);

  /* Increase counter by 1 */
  boot_counter++;

  // Print the counter to Serial Monitor
  //debugI.printf("Number of boots: %u\n", boot_counter);

  // Store the counter to the Preferences
  preferences.putUInt("boot_counter", boot_counter);

  // Close the Preferences
  preferences.end();
}

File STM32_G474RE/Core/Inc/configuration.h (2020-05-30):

/*******************************************************************
 * ALINEA_CONFIG.h
 *
 *  Created on: 26 avr. 2020
 *      Author: Jack Lestrohan
 *
 *******************************************************************/

#ifndef INC_CONFIGURATION_H_
#define INC_CONFIGURATION_H_

// IMPORTANT - uncomment this out in production!!!
//# define NDEBUG

#include "cmsis_os2.h"
#include <FreeRTOS.h>
#include <stdbool.h>

/* generic usage structs */
typedef StaticTask_t osStaticThreadDef_t; /* defined once here to lighten the code elsewhere */

#define FIRMWARE_VERSION	"AlineV 0.36"
//#define LCD_SHOW_EVENTS						/* uncomment = finite state information are displayed */
#define ESP32_VALID_UUID	"110976270102308"	/* ESP32 uuid, all commands coming from another uuid will be ignored */

/**
 * DEBUG CONFIGURATION
 * Sensors dbg_printf enable/disable
 */

/** sensors loggers **/
//#define DEBUG_HCSR04_ALL
//#define DEBUG_SYSTEMINFOS
//#define DEBUG_BMP280
//#define DEBUG_MG90S
//#define DEBUG_CMPS12
//#define DEBUG_ESP32_COMMAND_CHAIN
#define DEBUG_DATA_CONTROL


/** service activation **/
#define DEBUG_SERVICE_LCD_MENU
#define DEBUG_SERVICE_BUTTON
#define DEBUG_SERVICE_HCSR04
#define DEBUG_SERVICE_MG90S
#define DEBUG_SERVICE_ESP32_SERIAL
#define DEBUG_SERVICE_MOTORS
#define DEBUG_SERVICE_NAVCONTROL
#define DEBUG_SERVICE_UVLED
#define DEBUG_SERVICE_CMD_PARSER
#define DEBUG_SERVICE_BMP280
#define DEBUG_SERVICE_CMPS12
#define DEBUG_SERVICE_DATA_CTRL



/**
 * BEHAVIOUR CONTROL
 */
/* buttons debouncing */
#define BTN_DEBOUNCE_MS								150 /*  ms */

 /* on a forward motion, the rover will stop if the US BOTTOM sensor goes above the defined distance */
#define US_BOTTOM_SENSOR_HOLE_MIN_STOP_CM			10

/* what distance is considered by both angles of front distance sensing as "potential obstacle" */
#define US_ANGLE_MIN_STOP_CM						20	/* obstacle stop */
#define US_ANGLE_MIN_DANGER_CM						30	/* obstacle near danger */
#define US_ANGLE_MIN_WARNING_CM						40	/* obstacle potentially near, warning */

/* distance from which we stop the forward motion once an obstacle has been detected */
#define US_FRONT_MIN_STOP_CM						25	/* obstacle stop */
#define US_FRONT_MIN_DANGER_CM						30	/* obstacle near danger */
#define US_FRONT_MIN_WARNING_CM						40	/* obstacle potentially near, warning */

/* on a backward motion distance under which the rover will stop going backward */
#define US_REAR_MIN_STOP_CM							20

/* RX TX BUFFERS */
#define UART_DMA_BUFFER_SIZE 1024
#define PARSER_MESSAGE_LIST_SIZE 8
#define PARSER_MESSAGE_SIZE 1024
#define MAX_JSON_MSG_SIZE 512

#define MAX_HDLC_FRAME_LENGTH 512 /* this is the main frame length available */

/* Motors data */
#define MOTORS_DEFAULT_FW_SPEED			25
#define MOTORS_DEFAULT_WARNING_SPEED	17
#define MOTORS_DEFAULT_DANGER_SPEED		15
#define MOTORS_DEFAULT_TURN_SPEED		17
#define MOTORS_DEFAULT_BW_SPEED			20
#define MOTORS_DEFAULT_CORRECT_BIAS				4


/**
 * FEW HANDY MACROS
 */
#define MUTEX_MOTORDATA_TAKE 	osMutexAcquire(mMotorDataMutex, osWaitForever);
#define MUTEX_MOTORDATA_GIVE	osMutexRelease(mMotorDataMutex);
#define MUTEX_CMPS12_TAKE		osMutexAcquire(mCMPS12_SensorDataMutex, osWaitForever);
#define MUTEX_CMPS12_GIVE		osMutexRelease(mCMPS12_SensorDataMutex);
#define MUTEX_HCSR04_TAKE  		osMutexAcquire(mHR04_SensorsDataMutex, osWaitForever);
#define MUTEX_HCSR04_GIVE		osMutexRelease(mHR04_SensorsDataMutex);
#define MUTEX_UVLED_TAKE		osMutexAcquire(mUvLedStatusMutex, osWaitForever);
#define MUTEX_UVLED_GIVE		osMutexRelease(mUvLedStatusMutex);
#define MUTEX_NAVSTATUS_TAKE	osMutexAcquire(mCurrentNavStatusMutex, osWaitForever);
#define MUTEX_NAVSTATUS_GIVE	osMutexRelease(mCurrentNavStatusMutex);
#define MUTEX_BME280_TAKE		osMutexAcquire(mBMP280_DataMutex, osWaitForever);
#define MUTEX_BME280_GIVE		osMutexRelease(mBMP280_DataMutex);
#define MUTEX_SERVO_TAKE		osMutexAcquire(mServoPositionMutex, osWaitForever);
#define MUTEX_SERVO_GIVE		osMutexRelease(mServoPositionMutex);
#define MUTEX_LCD_TAKE			osMutexAcquire(mLCDScreenMutex, osWaitForever);
#define MUTEX_LCD_GIVE			osMutexRelease(mLCDScreenMutex);
#define MUTEX_HDLC_GIVE			osMutexRelease(mHdlcProtocolMutex);
#define MUTEX_HDLC_TAKE			osMutexAcquire(mHdlcProtocolMutex, osWaitForever);
#define MUTEX_RING_BUFF_TAKE	osMutexAcquire(mUartRingBufferMutex, osWaitForever);
#define MUTEX_RING_BUFF_GIVE	osMutexRelease(mUartRingBufferMutex);
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

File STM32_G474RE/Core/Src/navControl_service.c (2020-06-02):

/*******************************************************************
 * navControl_service.c
 *
 *  Created on: 2 mai 2020
 *      Author: Jack Lestrohan
 *
 *******************************************************************/

#include "navControl_service.h"
#include "main.h"
#include "HCSR04_service.h"
#include <stdlib.h>
#include "configuration.h"
#include "MG90S_service.h"
#include "printf.h"
#include "MotorsControl_service.h"
#include "CMPS12_service.h"
#include "uvLed_service.h"
#include <stdio.h>
#include <stdbool.h>
#include "IRQ_Handler.h"
#include "lcdMenu_service.h"

#define NUMBER_INIT_ATTEMPTS 2 /* how many trimes we retry before taking an action of avoidance */

static osMutexId_t mCurrentNavStatusMutex;
static NavigationStatus_t xCurrentNavStatus;

/********************************************************************
 * Extern variables from the different sensors and devices
 */
osEventFlagsId_t xEventLcdDisplay; /*extern*/

MotorData_t MotorData; /* extern */

osMessageQueueId_t xQueueMg90sMotionOrder; /* extern */
osMessageQueueId_t xMessageQueueMotorMotion; /* extern */

/* mutexed variables */
osMutexId_t mHR04_SensorsDataMutex; /* extern */

CMPS12_SensorData_t CMPS12_SensorData; /* extern */
osMutexId_t mCMPS12_SensorDataMutex; /* extern */

/********************************************************************/

/* functions definitions */
static void _vServoLedMotionForwardRules();
static void _vServoLedMotionBackwardRules();
static void _vServoLedMotionIdleRules();
//static uint8_t _uCheckFrontDangerZone(HR04_SensorsData *sensorData);
static uint8_t uGetNewBearing(int16_t deviationDegrees,  uint16_t *bearing);
uint8_t u_is_ref_bearing_right_of_actual(uint16_t *ref_bearing, uint16_t *actual_bearing);
//static uint8_t _vMotionSeekEscapePath();

MotorData_t lastMotorData; /* extern - records the last before the last events */
osEventFlagsId_t xEventFlagNavControlMainComn;
osMessageQueueId_t xMessageQueueDecisionControlMainCom;

/* a few macros */
#define MC_MOTORS_FORWARD	(((MotorData.motorMotion_Left == MOTOR_MOTION_FORWARD) && (MotorData.motorMotion_Right == MOTOR_MOTION_FORWARD)) && \
		((MotorData.currentSpeedLeft > 0) && (MotorData.currentSpeedRight > 0)))

#define MC_MOTORS_BACKWARD	(((MotorData.motorMotion_Left == MOTOR_MOTION_BACKWARD) && (MotorData.motorMotion_Right == MOTOR_MOTION_BACKWARD)) && \
		((MotorData.currentSpeedLeft > 0) && (MotorData.currentSpeedRight > 0)))

#define MC_MOTORS_IDLE 		(((MotorData.motorMotion_Left == MOTOR_MOTION_IDLE) && (MotorData.motorMotion_Right == MOTOR_MOTION_IDLE)) && \
		((MotorData.currentSpeedLeft == 0) && (MotorData.currentSpeedRight == 0)))



/*********************************************************************/
/* NORMAL NAV MOTION CONTROL TASK DEFINITION */
/** This task controls juste the normal behaviour of the android according
 * to the current motion.... */
static osThreadId_t xNavControlNormalMotionTaskHandle;
static osStaticThreadDef_t NavControlNormalMotionTaControlBlock;
static uint32_t NavControlNormalMotionTaBuffer[256];
static const osThreadAttr_t NavControlNormalMotionTa_attributes = {
		.name = "NavControlNormalMotionTask",
		.stack_mem = &NavControlNormalMotionTaBuffer[0],
		.stack_size = sizeof(NavControlNormalMotionTaBuffer),
		.cb_mem = &NavControlNormalMotionTaControlBlock,
		.cb_size = sizeof(NavControlNormalMotionTaControlBlock),
		.priority = (osPriority_t) OSTASK_PRIORITY_NAVCONTROL_NORM_MOTION, };

/*********************************************************************/
/* DECISION CONTROL TASK DEFINITION */
/** This task controls the sequence of actions to undertake when any
 * special event occurs */
static osThreadId_t xNavDecisionControlTaskHandle;
static osStaticThreadDef_t xNavDecisionControlTaControlBlock;
static uint32_t xNavDecisionControlTaBuffer[256];
static const osThreadAttr_t xNavDecisionControlTa_attributes = {
		.name = "xNavDecisionControlTask",
		.stack_mem = &xNavDecisionControlTaBuffer[0],
		.stack_size = sizeof(xNavDecisionControlTaBuffer),
		.cb_mem = &xNavDecisionControlTaControlBlock,
		.cb_size = sizeof(xNavDecisionControlTaControlBlock),
		.priority = (osPriority_t) OSTASK_PRIORITY_NAVCONTROL_DECISION, };


/**
 * Main Nav Service Task - This task controls the behaviour of the robot according to any motion
 * @param vParameters
 */
static void vNavControlNormalMotionTask(void *vParameters)
{
	printf("Starting Navigation Control task...\n\r");

	uint16_t xCurrentBearing, xDestinationBearing;
	//NavigationStatus_t lastNavigationStatus; /* used to keep track of the last known state, ie: turning motion */
	MotorMotion_t motorMotion;

	for (;;)
	{

		/** Lets's get a copy of some data structs and update them constantly  */
		MUTEX_CMPS12_TAKE
		xCurrentBearing = CMPS12_SensorData.CompassBearing;
		MUTEX_CMPS12_GIVE

		/** FINITE STATE MACHINE **/
		switch (xCurrentNavStatus) {

		/*---------------------------------------------------------------------------------------------------- */
		/* TRAJECTORY CORRECTION MODE */
		/*---------------------------------------------------------------------------------------------------- */
		case NAV_STATUS_CORRECT_HEADING:

			motorMotion = u_is_ref_bearing_right_of_actual(&xDestinationBearing, &xCurrentBearing)
			? MOTOR_MOTION_FORWARD_LEFT : MOTOR_MOTION_FORWARD_RIGHT;
			osMessageQueuePut(xQueueMotorMotionOrder, &motorMotion, 0U, osWaitForever);

			MUTEX_NAVSTATUS_TAKE
			xCurrentNavStatus = NAV_STATUS_EXPLORING; /* back to exploring */
			MUTEX_NAVSTATUS_GIVE
			break;

			/*---------------------------------------------------------------------------------------------------- */
			/* EXPLORING MODE */
			/*---------------------------------------------------------------------------------------------------- */
		case NAV_STATUS_EXPLORING:

			/* we try to keep the heading */
			if (xCurrentBearing != xDestinationBearing) {
				MUTEX_NAVSTATUS_TAKE
				xCurrentNavStatus = NAV_STATUS_CORRECT_HEADING; /* back to exploring */
				MUTEX_NAVSTATUS_GIVE
			}

			/* front sensor data check, if we hit an obstacle, we stop and enter avoiding mode */

			if (HCSR04_get_dist_front() < US_FRONT_MIN_STOP_CM) {

				MUTEX_NAVSTATUS_TAKE
				xCurrentNavStatus = NAV_STATUS_AVOIDING; /* we set that flag to be able to try to avoid the obstacle */
				MUTEX_NAVSTATUS_GIVE

				printf("Obstacle detected front: %d cm\n\r", HCSR04_get_dist_front());
				printf("Entering AVOIDING mode..\n\r");
			} else

				/* front sensor detected something at warning zone, we reduce speed */
				if (HCSR04_get_dist_front() < US_FRONT_MIN_DANGER_CM) {
					printf("Warning ahead distance: %d cm\n\r", HCSR04_get_dist_front());
					motorMotion = MOTOR_SPEED_REDUCE_DANGER;
					osMessageQueuePut(xQueueMotorMotionOrder, &motorMotion, 0U, osWaitForever);
				} else {
					/* or we set back to front if we're ok */
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

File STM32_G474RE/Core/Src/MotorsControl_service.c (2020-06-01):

/*******************************************************************
 * MotorsControl_service.c
 *
 *  Created on: Apr 18, 2020
 *      Author: Jack Lestrohan
 *
 *******************************************************************/

#include <FreeRTOS.h>
#include "cmsis_os2.h"
#include "configuration.h"
#include <stdlib.h>
#include "MotorsControl_service.h"
#include "gpio.h"
#include "tim.h"
#include "printf.h"
#include "main.h"
#include "MG90S_service.h"
#include <assert.h>

typedef StaticTask_t osStaticThreadDef_t;
static osThreadId_t xMotorsControlTaskHnd;
static uint32_t xMotorsControlTaBuffer[256];
static osStaticThreadDef_t xMotorsControlTaControlBlock;
static const osThreadAttr_t xMotorsControlTa_attributes = {
		.name = "MotorsControlServiceTask",
		.priority = (osPriority_t) osPriorityLow1,
		.stack_mem = &xMotorsControlTaBuffer[0],
		.stack_size = sizeof(xMotorsControlTaBuffer),
		.cb_mem = &xMotorsControlTaControlBlock,
		.cb_size = sizeof(xMotorsControlTaControlBlock),
};

/* extern variables */
osMessageQueueId_t xQueueMotorMotionOrder;
osMutexId_t mMotorDataMutex, mLastMotorDataMutex;
MotorData_t MotorData, lastMotorData = {MOTOR_MOTION_IDLE, MOTOR_MOTION_IDLE, 0,0};



/* functions definitions */
static void motorsSetMotionIdle(MotorData_t *data);
static void motorSetMotionForward(MotorData_t *data, uint8_t speed);
static void motorSetMotionBackward(MotorData_t *data, uint8_t speed);
static void MotorSetSpeed(MotorData_t *data, uint8_t speed_left, uint8_t speed_right);
static void motorSetMotionTurnRight(MotorData_t *data, uint8_t speed_left, uint8_t speed_right);
static void motorSetMotionTurnLeft(MotorData_t *data, uint8_t speed_left, uint8_t speed_right);


/**
 * Motors Control main task
 * @param argument
 */
static void vMotorsControlTaskStart(void *vParameters)
{
	printf("Starting Motors Control Task...\n\r");

	mMotorDataMutex = osMutexNew(NULL);
	mLastMotorDataMutex = osMutexNew(NULL);

	xQueueMotorMotionOrder = osMessageQueueNew(10, sizeof(uint8_t), NULL);
	if (xQueueMotorMotionOrder == NULL) {
		printf("Motors Message Queue Initialization Failed\n\r");
		Error_Handler();
	}

	HAL_TIM_PWM_Start(&htim16, TIM_CHANNEL_1);
	HAL_TIM_PWM_Start(&htim17, TIM_CHANNEL_1);

	/* initializes PWM duties to 0 for now (idle) */
	htim16.Instance->CCR1 = 0;
	htim17.Instance->CCR1 = 0;


	MotorMotion_t msgOrder;

	for (;;)
	{
		/* event flag motors active - these flags are just disposable events flags */
		osMessageQueueGet(xQueueMotorMotionOrder, &msgOrder, NULL, osWaitForever);

		switch (msgOrder) {
		case MOTOR_MOTION_FORWARD:
			motorSetMotionForward(&MotorData, MOTORS_DEFAULT_FW_SPEED);
			break;

		case MOTOR_MOTION_BACKWARD:
			motorSetMotionBackward(&MotorData, MOTORS_DEFAULT_BW_SPEED);
			break;

		case MOTOR_MOTION_IDLE:
			motorsSetMotionIdle(&MotorData);
			break;
		case MOTOR_SPEED_NORMAL:
			MotorSetSpeed(&MotorData, MOTORS_DEFAULT_FW_SPEED, MOTORS_DEFAULT_FW_SPEED);
			break;
		case MOTOR_SPEED_REDUCE_DANGER:
			MotorSetSpeed(&MotorData, MOTORS_DEFAULT_DANGER_SPEED, MOTORS_DEFAULT_DANGER_SPEED);
			break;
		case MOTOR_SPEED_REDUCE_WARNING:
			MotorSetSpeed(&MotorData, MOTORS_DEFAULT_WARNING_SPEED, MOTORS_DEFAULT_WARNING_SPEED);
			break;
		case MOTOR_MOTION_TURN_RIGHT:
			motorSetMotionTurnRight(&MotorData, MOTORS_DEFAULT_TURN_SPEED, MOTORS_DEFAULT_TURN_SPEED);
			break;
		case MOTOR_MOTION_TURN_LEFT:
			motorSetMotionTurnLeft(&MotorData, MOTORS_DEFAULT_TURN_SPEED, MOTORS_DEFAULT_TURN_SPEED);
			break;
		case MOTOR_MOTION_FORWARD_RIGHT: //TODO: add PID here, the more/less we reduce distance against wall the more we derive each caterp speed */
			MotorSetSpeed(&MotorData, MotorData.currentSpeedLeft + 2, MotorData.currentSpeedRight - 2);
			break;
		case MOTOR_MOTION_FORWARD_LEFT: //TODO: add PID here, the more/less we reduce distance against wall the more we derive each caterp speed */
			MotorSetSpeed(&MotorData, MotorData.currentSpeedLeft - 2, MotorData.currentSpeedRight + 2);
			break;
		case MOTOR_MOTION_CORRECT_RIGHT:
			MotorSetSpeed(&MotorData, MotorData.currentSpeedLeft + MOTORS_DEFAULT_CORRECT_BIAS, MotorData.currentSpeedRight - MOTORS_DEFAULT_CORRECT_BIAS);
			break;
		case MOTOR_MOTION_CORRECT_LEFT:
			MotorSetSpeed(&MotorData, MotorData.currentSpeedLeft - MOTORS_DEFAULT_CORRECT_BIAS, MotorData.currentSpeedRight + MOTORS_DEFAULT_CORRECT_BIAS);
			break;
		default:
			motorsSetMotionIdle(&MotorData);
			break;
		}

		osDelay(1);
	}
	osThreadTerminate(xMotorsControlTaskHnd);
}

/**
 * Initialize the whole service, tasks and stuff
 * @return
 */
uint8_t uMotorsControlServiceInit()
{
	/* creation of the MotorsControl_task */
	xMotorsControlTaskHnd = osThreadNew(vMotorsControlTaskStart, NULL, &xMotorsControlTa_attributes);
	if (xMotorsControlTaskHnd == NULL) {
		printf("MotorsControl Task Initialization Failed\n\r");
		Error_Handler();
		return (EXIT_FAILURE);
	}

	printf("Initializing Motors Control Service... Success!\n\r");
	return (EXIT_SUCCESS);
}

/**
 * sets motor(s) speed to the target pace using motionchange rate
 * @param speed (0-100)
 */
static void MotorSetSpeed(MotorData_t *data, uint8_t speed_left, uint8_t speed_right)
{
	/* let's clamp the values to avoid overflow */
	speed_left = speed_left > 100 ? 100 : speed_left;
	speed_right = speed_right > 100 ? 100 : speed_right;

	/* if speed <= 0 we deactivate the PWM timers to save energy, motor after motor */
	if (speed_left <= 0) {
		HAL_TIM_PWM_Stop(&htim16, TIM_CHANNEL_1);
	} else {
		HAL_TIM_PWM_Start(&htim16, TIM_CHANNEL_1);
		htim16.Instance->CCR1 = speed_left;
	}

	if (speed_right <= 0)  {
		HAL_TIM_PWM_Stop(&htim17, TIM_CHANNEL_1);
	} else {
		HAL_TIM_PWM_Start(&htim17, TIM_CHANNEL_1);
		htim17.Instance->CCR1 = speed_right;
	}

	/* save the current values into the data struct */
	MUTEX_MOTORDATA_TAKE
	lastMotorData = *data; /* backup the data into the last known values struct */

	data->currentSpeedLeft = speed_left; /* records the current speed */
	data->currentSpeedRight = speed_right;
	MUTEX_MOTORDATA_GIVE
}

/**
 * Sets LN298 GPIO controls for forward motion
 * One speed for two motors, we are supposed to go forward
 */
static void motorSetMotionForward(MotorData_t *data, uint8_t speed)
{
	HAL_GPIO_WritePin(GPIOA, MOTOR1_IN1_Pin, GPIO_PIN_RESET);
	HAL_GPIO_WritePin(GPIOA, MOTOR1_IN2_Pin, GPIO_PIN_SET);
	HAL_GPIO_WritePin(GPIOC, MOTOR2_IN3_Pin, GPIO_PIN_RESET);
	HAL_GPIO_WritePin(GPIOD, MOTOR2_IN4_Pin, GPIO_PIN_SET);

	/* now we set the right values into the main motors control struct */
	MUTEX_MOTORDATA_TAKE
	lastMotorData = *data; /* backup the data into the last known values struct */

	data->motorMotion_Left = MOTOR_MOTION_FORWARD;
	data->motorMotion_Right = MOTOR_MOTION_FORWARD;
	MUTEX_MOTORDATA_GIVE

	/* set the required speed */
	MotorSetSpeed(data, speed, speed);
}
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

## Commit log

2020-03-20 added button handler support files
2020-03-20 added speed sensor handler
2020-03-21 fixed sensor acquisition
2020-03-21 Added support for all Speed Sensors
2020-03-27 Added buzzer support files
    [Alinea_STM32_474RE.ioc, main.h]
2020-03-27 added SDCard SPI support
2020-03-28 Mounting SD Card working
2020-03-28 minor post merge fixes
    [Alinea_STM32_474RE.ioc]
2020-03-28 post merge minor fixes
    [Alinea_STM32_474RE.ioc, main.h]
2020-03-29 removed buzzer pwm timer
    [Alinea_STM32_474RE.ioc]
2020-04-02 Add PWM HC-SR04 timer
2020-04-03 Added debug prints
2020-04-03 Added UART IRQ
2020-04-04 Added vl53l0X Drivers files
2020-04-04 Added drivers support functions
2020-04-08 #29 added semaphore on UART
2020-04-10 #21 mde service full RTOS compliant (capture timers)
2020-04-10 #35 removed invalid values when sensor is far away from obstacle
2020-04-11 Added more drivers functions (unstable)
2020-04-12 #21 replaced blocking µs timer by PWM timer
    [Alinea_STM32_474RE.ioc, main.h, sensor_hr04_service.c]
2020-04-12 Added STM32G474RE Configuration Reports
2020-04-12 Added Ftitzing files
    [Pinout and Schematics.fzz]
2020-04-12 Improved Timer Usage
    [Pinout and Schematics.fzz]
2020-04-12 #37 added second HC-SR04 Ultrasonic Sensor
    [Pinout and Schematics.fzz]
2020-04-13 #39 Added third sonar support
2020-04-13 Updated schematics
    [Pinout and Schematics.fzz]
2020-04-18 Added Motors control service files
2020-04-20 Added Wifi status LED
2020-04-22 Switched to ESP32
2020-04-25 Added HC-SR04 servo control skeleton files
2020-04-25 #6 restored wifi music on ESP32
2020-04-25 Updated to reflect new ESP32 pinout
    [Pinout and Schematics.fzz]
2020-04-26 Added Motors Connexions + PWM TIM
2020-04-26 removed buzzer service (handled by ESP32 now)
2020-04-26 Dde
    Added motors control basic demo
2020-04-27 Reworked command parsing process
    [main.cpp]
2020-04-28 #52 Added servo control for front HC-SR04
2020-04-28 #42 implemented ESP STM32 UART basic communication
2020-04-28 minor changes
    [configuration_esp32.h]
2020-04-29 Added lighter printf/sprintf
2020-04-29 minor fixes
    [configuration.h]
2020-04-30 Added servo control flags
2020-04-30 Minor features added
    [configuration.h]
2020-05-01 Added second button logic
    [configuration.h]
2020-05-02 #20 reworked LCD factory
    [configuration.h]
2020-05-02 Improved motors control
2020-05-02 Updated + bug fix OTA #51
    [ota_service.cpp]
2020-05-02 Updated navigation & motion control
    [configuration.h]
2020-05-02 #42 Implemented Com Protocol
    [configuration.h]
2020-05-04 DMA UART from ESP to STM
    Optimized, no protocol
2020-05-04 Add LED3 (mcu1-mcu2 DMA UART Activity)
    [configuration.h]
2020-05-05 Added Uart Ring Buffer
2020-05-05 Inserted a return to avoid modifying code
2020-05-05 Slowed test UART transmission a bit to verify STM uart led is ok
2020-05-06 #42 Finalized UART HDCL Prot Bi directional communication
2020-05-06 #55 added enab ling/disabling sensors vs motors motion direction
2020-05-06 Many fixes
    [configuration.h, configuration_esp32.h]
2020-05-07 Added last status struct
    [configuration.h]
2020-05-07 Add debug configuration control
    [configuration.h]
2020-05-07 Updated a few definitions
    [configuration.h]
2020-05-07 Added Sysinfo service
    [configuration.h]
2020-05-07 Removed pressure sensor (no use)
2020-05-07 Added UV LED Service
    [configuration.h]
2020-05-08 Added DEBUG flags
    [configuration.h]
2020-05-09 Motors Control fixes
2020-05-09 Improved navigation control
    [configuration.h]
2020-05-09 Added IA functions & demo behaviour
    [configuration.h]
2020-05-10 Move setting to general config file
    [configuration.h]
2020-05-10 Whole bunch of fixes for a working status
    [configuration.h]
2020-05-12 Enforced working protocoled communication between both MCU's
    [configuration.h]
2020-05-12 Added minimal IA
    [configuration.h]
2020-05-12 Fixed servo positions
2020-05-13 Fixed little obstacle detection bug
    [Alinea_STM32_474RE.ioc, MG90S_service.h, MotorsControl_service.c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]
2020-05-13 Removed service for a much better sensor
2020-05-14 Added BMP280 support files
    Working as intended
    [configuration.h]
2020-05-14 Auto stash before merge of "dev" and "origin/dev"
    [configuration.h]
2020-05-15 Buf fix #40 and improved navigation decision taking
    [MG90S_service.h, navControl_service.c]
2020-05-15 Switched from heap_4 to heap_1 to accomodate more static tasks
2020-05-15 Added working bearing polling
    [configuration.h]
2020-05-15 Added the rest of the sensor datas
2020-05-17 Led command library bug workaround
2020-05-17 Cancelled gitmodules work
    Path incompatibilities with ESP32/STM32 shared workspace
2020-05-17 Added submodules at the right places
    Tweaked to make submodules be included in the stm32 workspace
2020-05-17 Added working hdlc bi directional communication
    [configuration.h]
2020-05-18 Added STM32 uuid check (stub) on serial com stm->esp
    [configuration_esp32.h]
2020-05-19 Added wrong argument melody
    [buzzer_service.cpp]
2020-05-19 Fixed #72
    [configuration_esp32.h]
2020-05-20 Add MQTT AWS working connexion
    [configuration_esp32.h]
2020-05-20 Add MQTT AWS working connexion #49
    [configuration_esp32.h]
2020-05-23 removed sd driver temporarily
2020-05-23 Minor stability fixes
    [configuration.h]
2020-05-24 Navigation fixes
    [configuration.h]
2020-05-24 Reworked IRQ hcsr data grabbing
    [navControl_service.c]
2020-05-24 Added rear collision check
    [navControl_service.c]
2020-05-24 Added phil ekstrom filter algorithm to filter out outliers
2020-05-25 Removed last bugs and flickering
    [configuration.h]
2020-05-25 Many speed improvements
    [configuration.h]
2020-05-25 IA adjustments
    [configuration.h]
2020-05-26 Moved motors config to config file
    [configuration.h]
2020-05-28 Replaced ESP8266 by ESP32
    [main.cpp, stm32Serial_service.cpp]
2020-05-28 UART speed to 115200
    [configuration.h]
2020-05-28 Servo now goes to center at startup
2020-06-02 Reworked C encapsulation rules
    [navControl_service.c]
